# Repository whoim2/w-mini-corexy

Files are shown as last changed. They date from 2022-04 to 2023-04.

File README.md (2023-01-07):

# w-mini-corexy
small&amp;simple coreXY printer with low weight feeder and linear shafts, 238x188x150 workplace

MOD by Ahiko (recommended, standart linear bearings):
[link](https://github.com/whoim2/w-mini-corexy/tree/main/Ahiko)
or STEP assembly for solidworks:
[link](https://github.com/whoim2/w-mini-corexy/raw/main/Ahiko/Assembly1.STEP.zip)

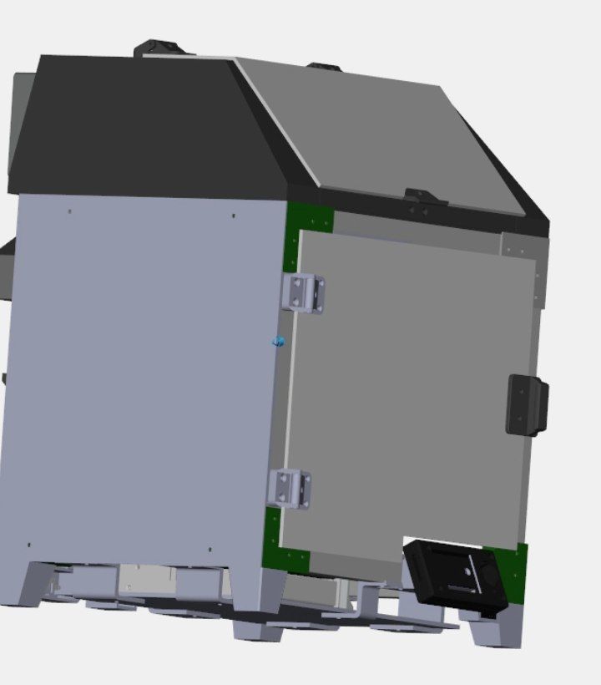
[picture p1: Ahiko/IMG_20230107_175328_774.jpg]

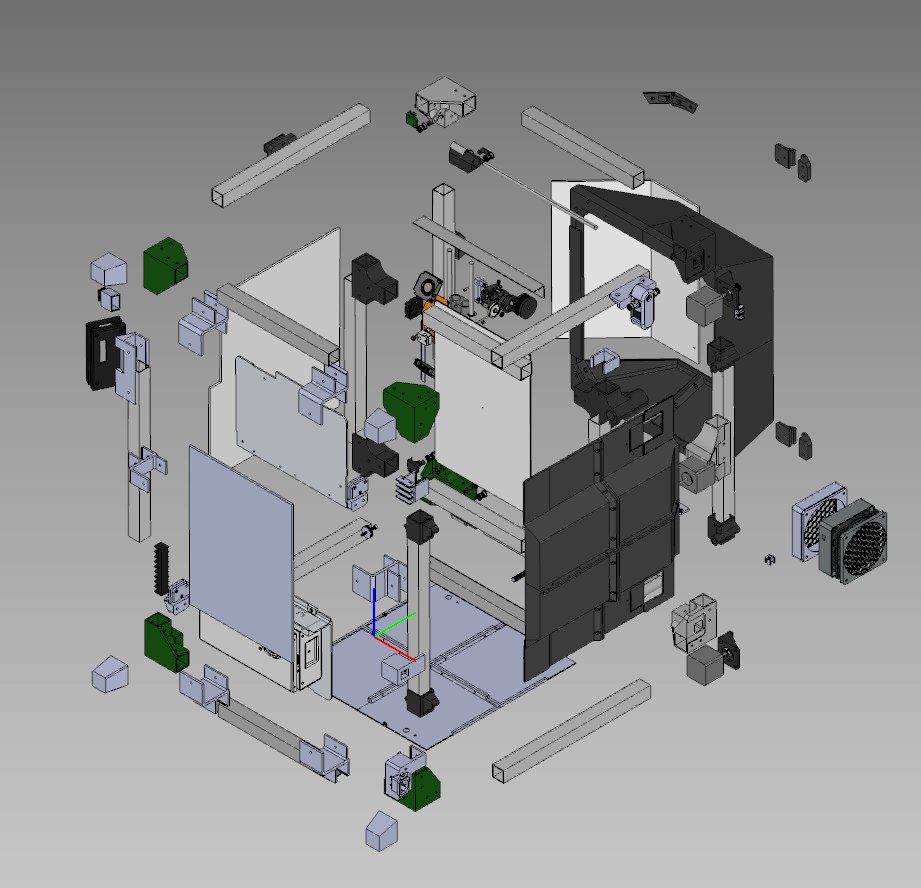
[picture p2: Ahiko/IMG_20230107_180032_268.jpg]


Original cloud files - last versions: https://disk.yandex.ru/d/OpFREoRlxXPGTw

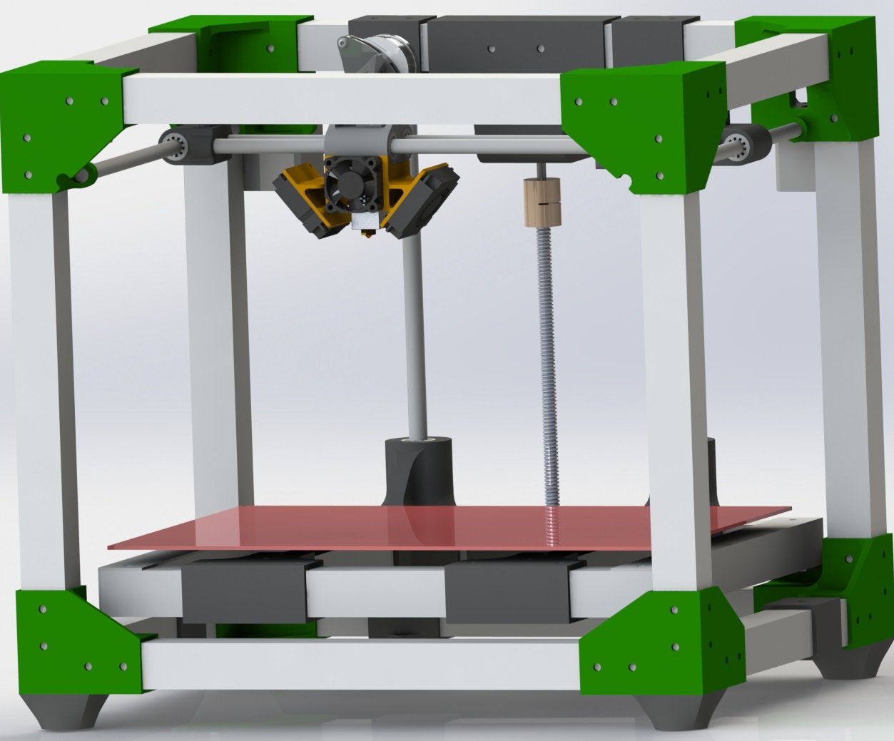
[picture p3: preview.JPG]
preview


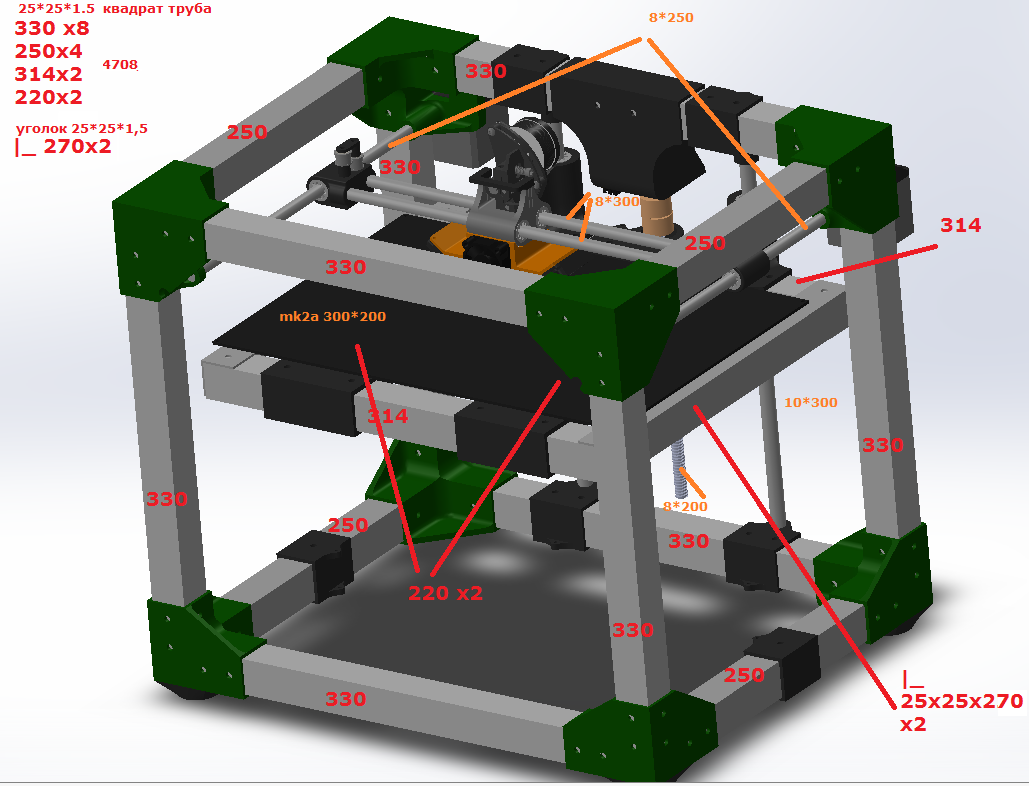
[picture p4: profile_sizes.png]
sizes


k3d mini feeder: https://github.com/dmitry-sorkin/k3d-minifeeder

[https://youtu.be/Zjof3f4mJVk](https://www.youtube.com/watch?v=Zjof3f4mJVk)

Bearings: f623zz x16

shafts: d8 L250 x2; d8 L300 x2

steppers: nema17 17HS4401S x3; Q3948-60186 x1

screw: T8 4 lead 2 pitch, 200mm, x1

rivets: d4 L8 x120

aluminum profile: 25x25x1,5 5meters

heatblock: v5 16x16x12

cut e3dv6 radiator, drill 5.5mm hole, cut M6 thread. Use offcut steel bore 3mm heatbreak for mount sink in x-carriage and teflon tube 3/2mm from feeder to heatbreak.

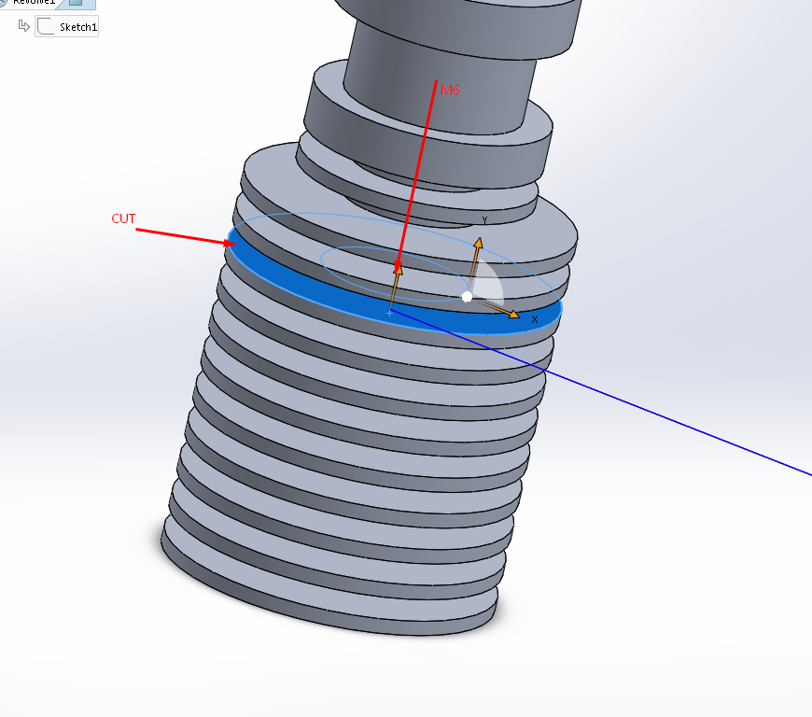
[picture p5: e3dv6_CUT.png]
cut


project in solid 2019

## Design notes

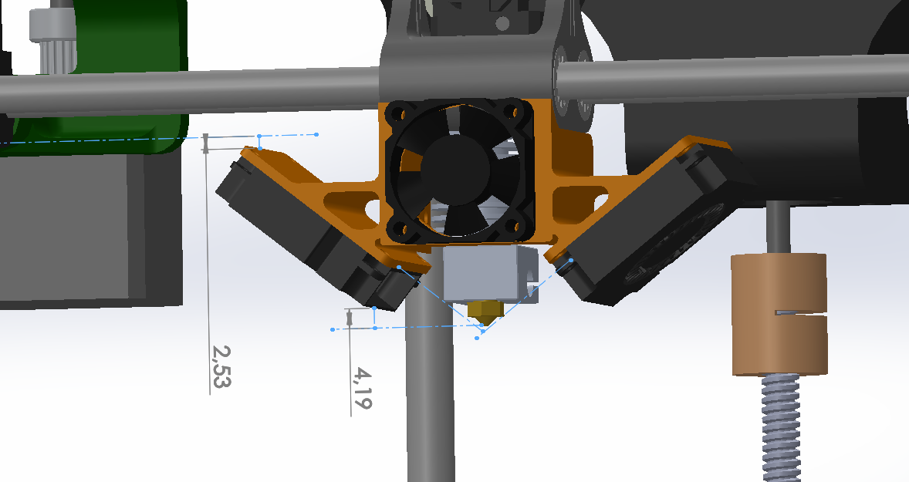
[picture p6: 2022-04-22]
Ahiko/Screenshot_1.png

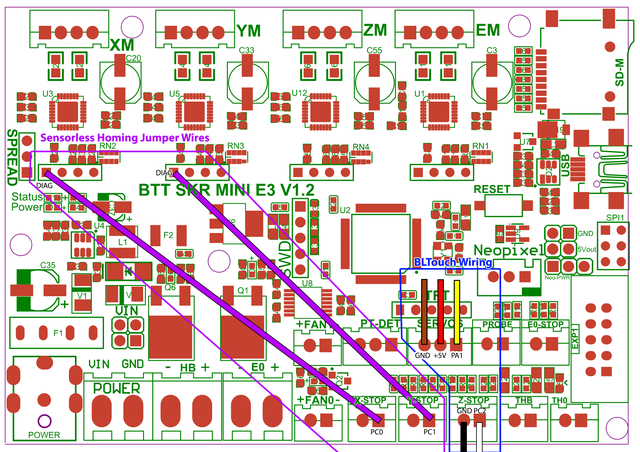
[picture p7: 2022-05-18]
klipper/skr-e3-sensorless.webp

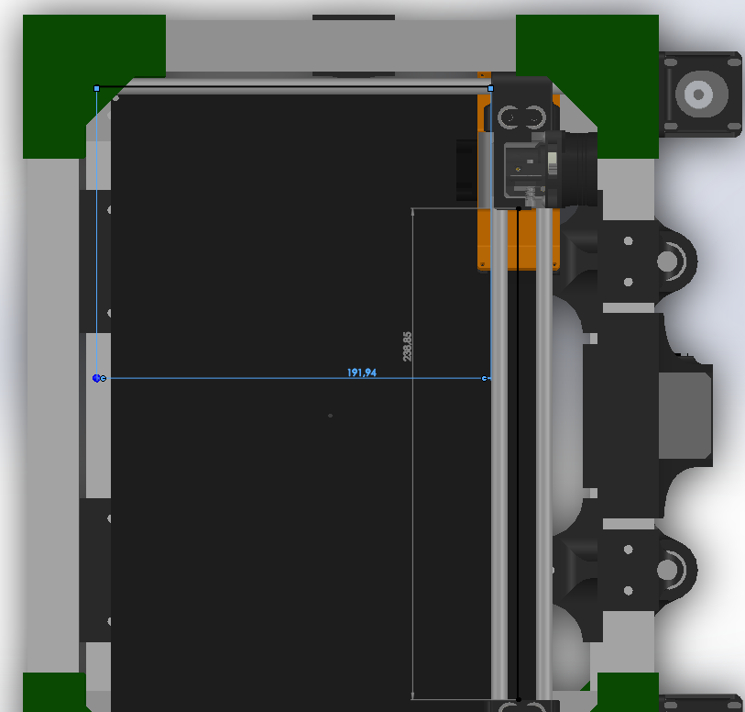
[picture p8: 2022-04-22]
Ahiko/Screenshot_2.png

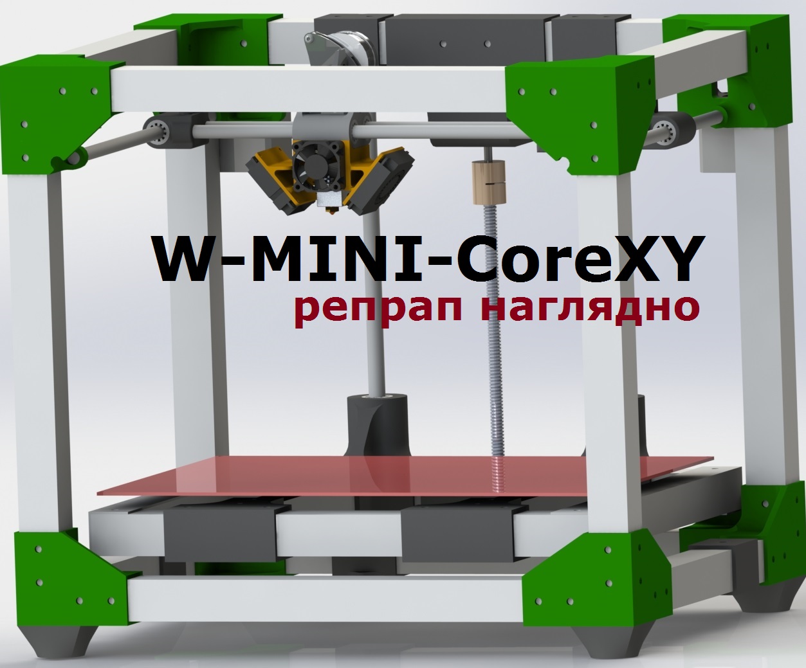
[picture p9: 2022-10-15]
Ahiko/preview_y.jpg

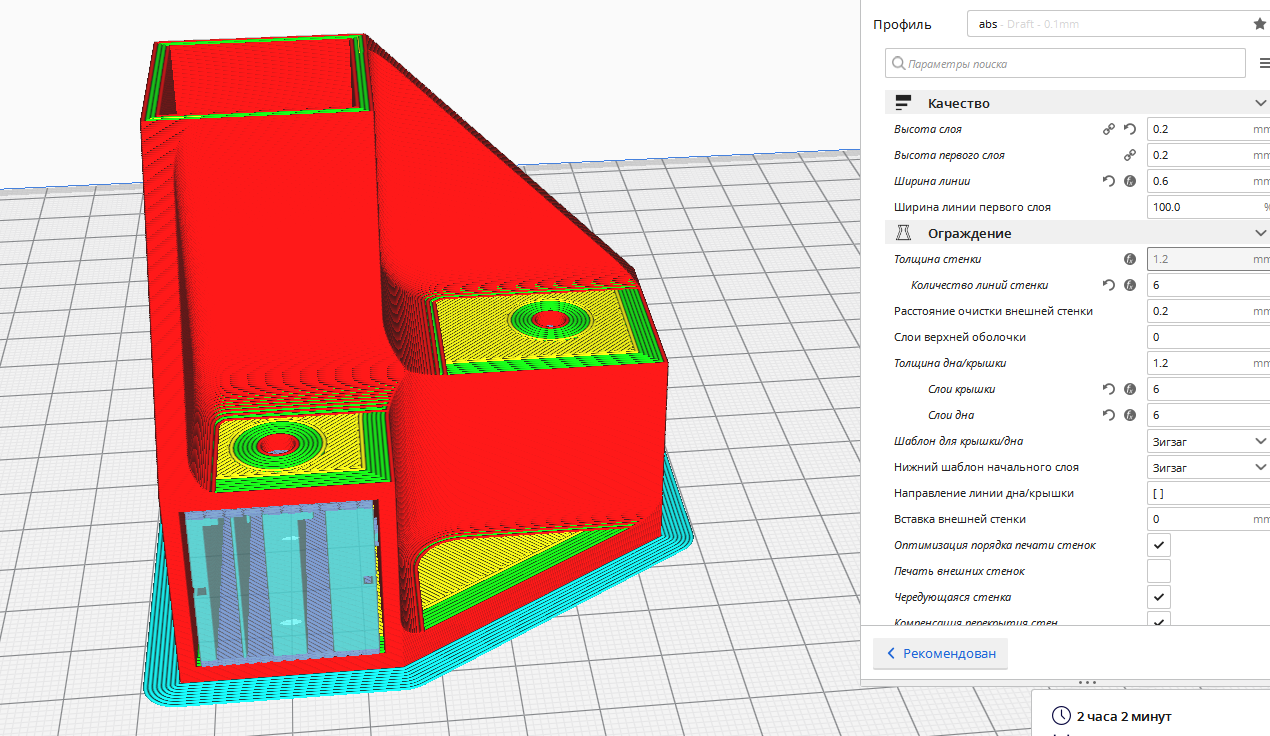
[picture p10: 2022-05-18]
Ahiko/Screenshot_3.png

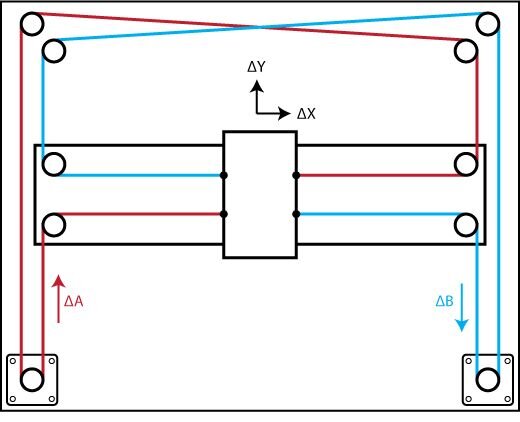
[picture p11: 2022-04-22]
Ahiko/corexy-reference_img_5eb0505acf645.jpg

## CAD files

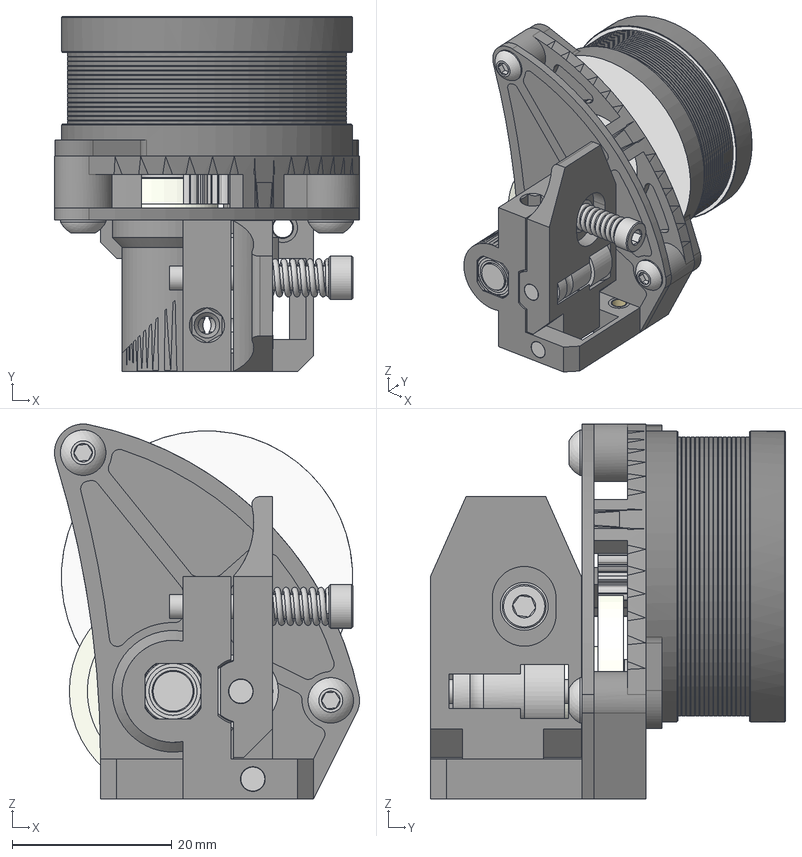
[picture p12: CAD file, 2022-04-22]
k3d-minifeeder-main/K3D Minifeeder assembly.stp
38.2 x 44.5 x 47.0 mm
MF-01b - Minifeeder back lite
MF-02b - Minifeeder front lite
Threaded insert M3x5 x 3
BMG stift 19mm x 2
Screw socket M3x20
Washer M3
BMG spring
Screw round M3x10 x 2
MF-03 - Minifeeder lever
MF-02 - Minifeeder front
MF-01 - Minifeeder back
BMG bearing x 2
Motor Nema14 L17
BMG motor gear
BMG small gear x 2

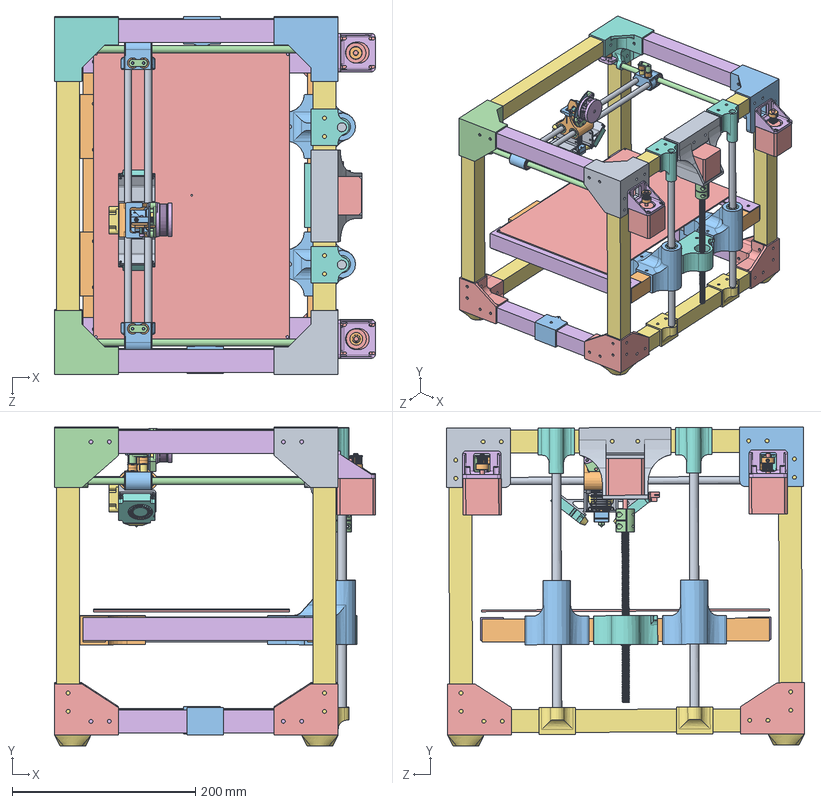
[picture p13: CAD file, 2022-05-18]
Assembly.SLDASM
350.4 x 348.1 x 390.7 mm
8x300 x 2
X_carriage
Y_carriage x 2
8x250 x 2
corner_25mm_bottom x 4
profile_sq_25x250 x 4
profile_sq_25x330 x 8
corner_25mm_top_front_1
corner_25mm_top_rear_2
f693zz x 16
corner_25mm_top_rear_1
corner_25mm_top_front_2
nema17 x 3
mot_xy_mount x 2
z_bottom_mount_linear x 2
z_top_mount_linear x 2
10x300 x 2
MF-01b - Minifeeder back lite.stp
MF-02b - Minifeeder front lite.stp
Threaded insert M3x5.stp x 3
BMG stift 19mm.stp x 2
Screw socket M3x20.stp
Washer M3.stp
BMG spring.stp
Screw round M3x10.stp x 2
MF-03 - Minifeeder lever.stp
MF-02 - Minifeeder front.stp
MF-01 - Minifeeder back.stp
BMG bearing.stp x 2
Motor Nema14 L17.stp
BMG motor gear.stp
BMG small gear.stp x 2
profile_sq_25x220 x 2
corner_25mm_Z x 2
corner_25mm_Z_bearing x 2
khop5x8
LeadScrew 8mm x 2mmPitch
LeadScrew Nut 8mm x 2mmPitch
foot x 4
mount_Z_t8nut
mount_Z_mot
profile_sq_25x314 x 2
universal_mount_25 x 2
lm8-38mm x 2
lm8-30mm x 2
front_roll_mount
bearing_roll x 4
lm10-70mm x 2
e3d-heatsink
e3d-heatbreak
e3d-heaterblock
e3d-nozzle-04
mk2a_300x200
angle_25x25_270 x 2
Fan 3010
4010blower x 2
fans_mount
GT2_16T x 2
X_carriage_topfix
bearing_roll2 x 2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

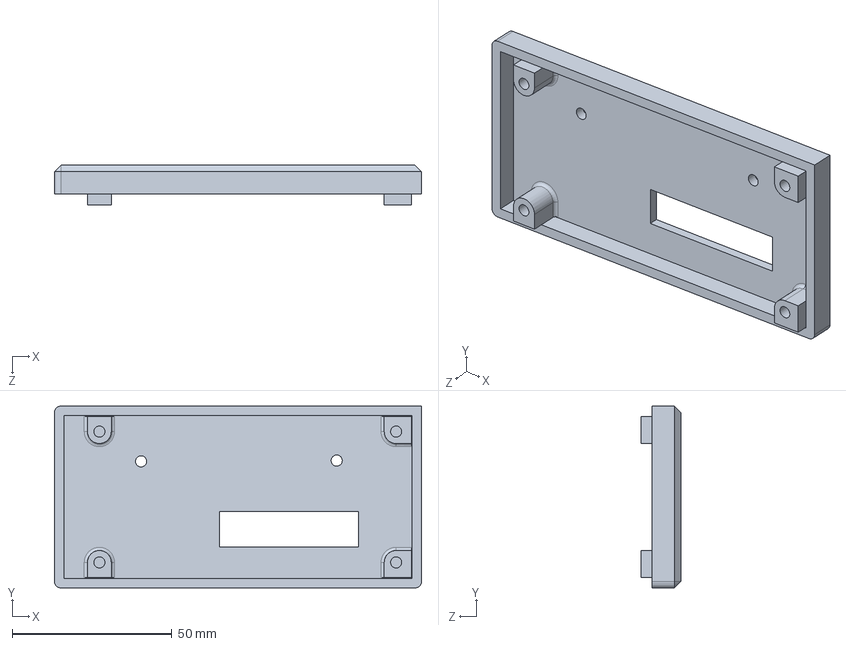
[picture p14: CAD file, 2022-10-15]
Ahiko/Сборка1.SLDASM
115.0 x 57.0 x 12.4 mm

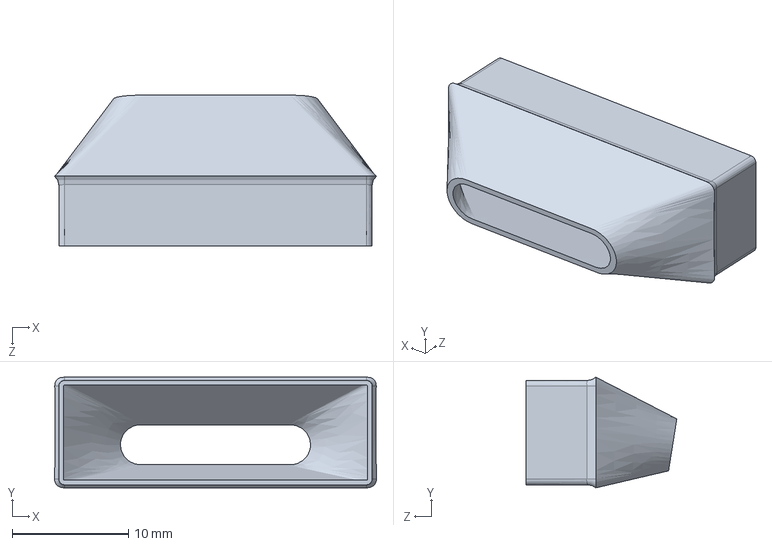
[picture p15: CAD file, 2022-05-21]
4010turbo_duct.SLDPRT
27.7 x 9.54 x 13.0 mm

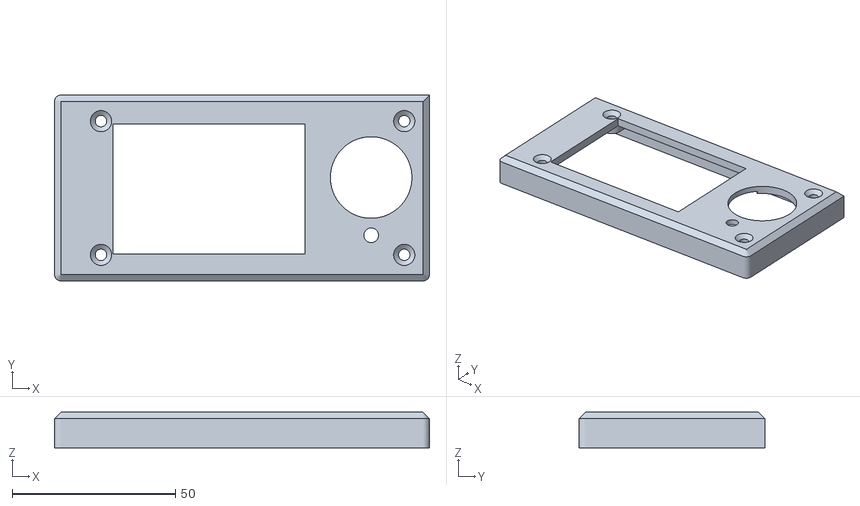
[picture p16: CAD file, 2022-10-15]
Ahiko/stl/Fysetc_Mini_12864_Mini_Front.stl
115.0 x 57.0 x 11.0

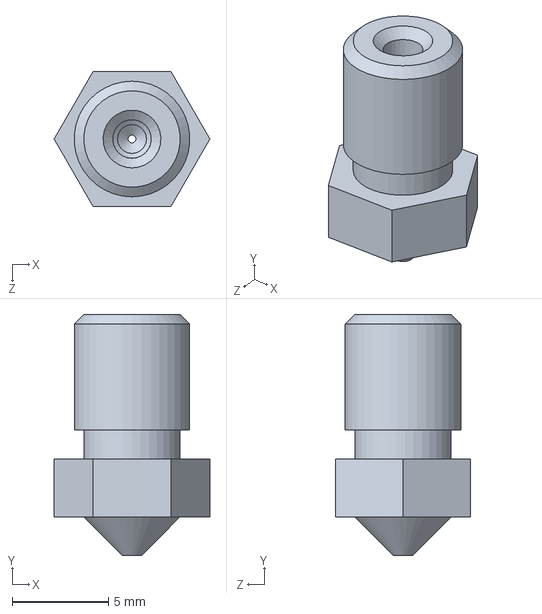
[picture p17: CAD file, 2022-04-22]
e3dv6/e3d-nozzle-04.SLDPRT
8.08 x 12.5 x 7.00 mm

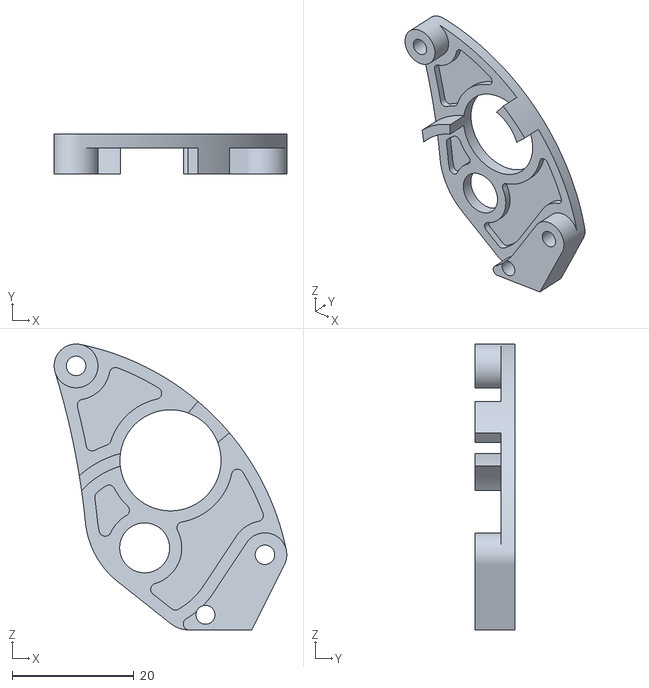
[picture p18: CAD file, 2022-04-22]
k3d-minifeeder-main/STL/K3D Minifeeder back.stl
38.2 x 6.50 x 47.0

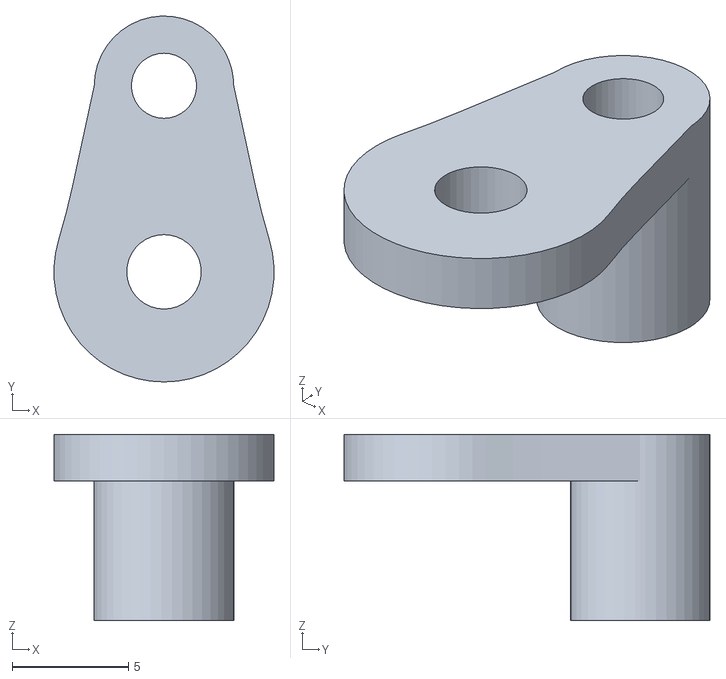
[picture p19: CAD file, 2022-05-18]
Ahiko/stl/pcb_mount.STL
9.46 x 15.7 x 8.00

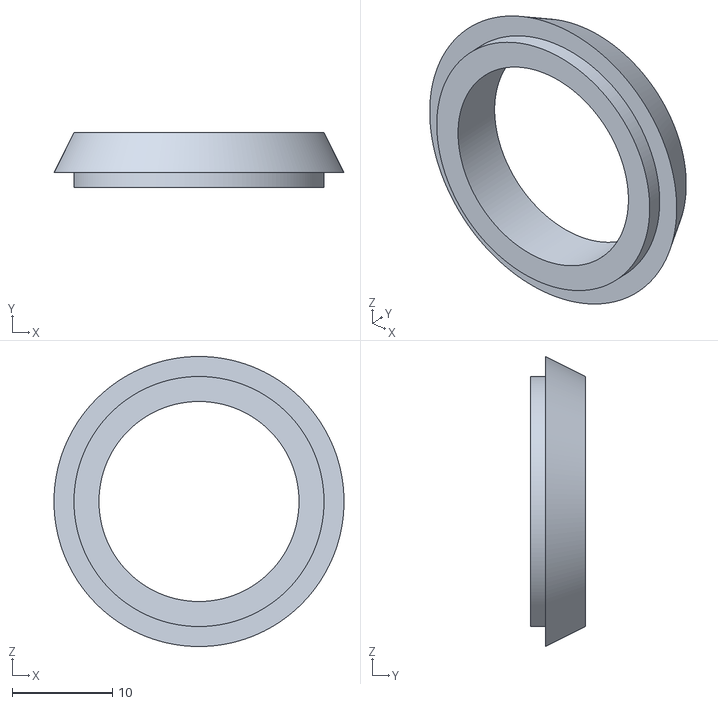
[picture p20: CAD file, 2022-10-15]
Ahiko/проставка.STL
29.0 x 5.50 x 29.0

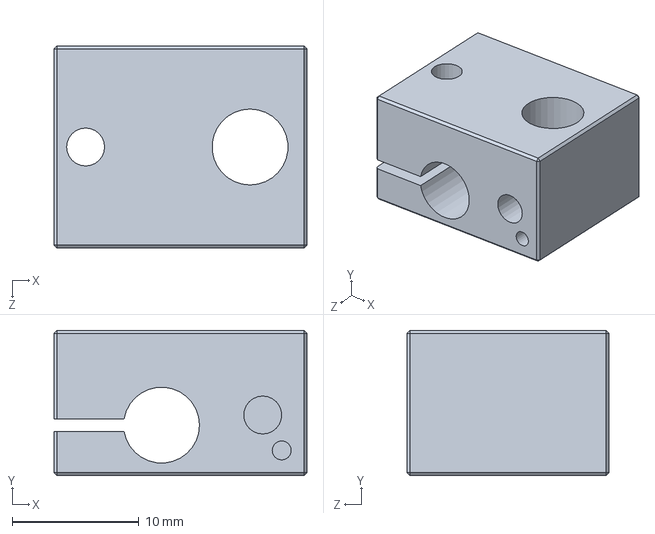
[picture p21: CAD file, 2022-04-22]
e3dv6/e3d-heaterblock.SLDPRT
20.0 x 11.5 x 16.0 mm

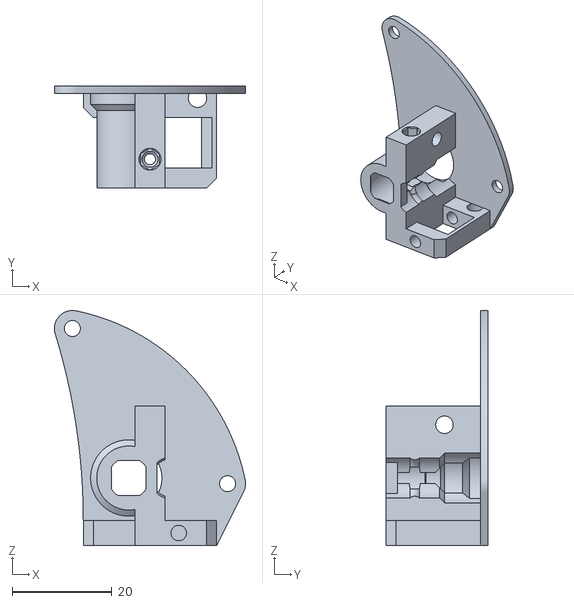
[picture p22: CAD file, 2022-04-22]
k3d-minifeeder-main/STL/K3D Minifeeder front.stl
38.2 x 20.5 x 47.0

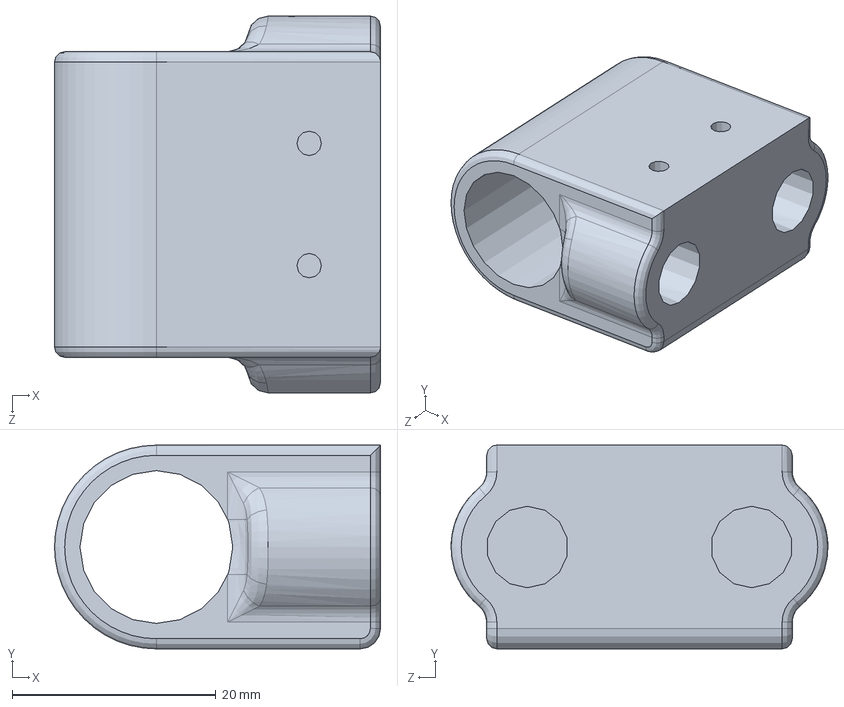
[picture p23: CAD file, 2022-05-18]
Y_carriage.SLDPRT
32.0 x 20.0 x 37.0 mm

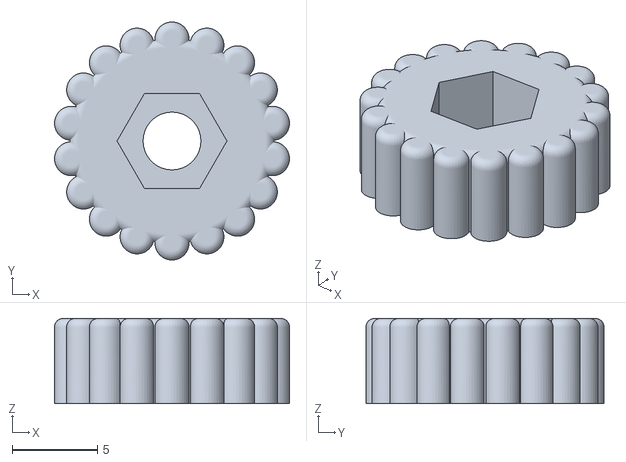
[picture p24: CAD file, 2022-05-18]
Ahiko/stl/ручка_стол.STL
13.8 x 14.0 x 5.00

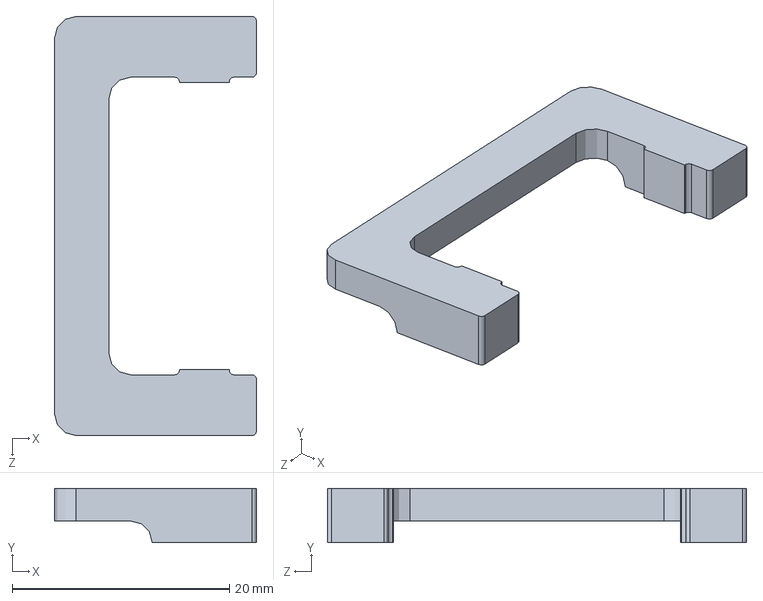
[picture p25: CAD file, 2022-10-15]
Ahiko/X_carriage_topfix.SLDPRT
18.6 x 5.00 x 38.6 mm

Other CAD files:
Ahiko/K3D Minifeeder assembly.stp.SLDASM
Ahiko/Fysetc Mini 12864 v1.step.SLDASM
e3dv6/e3d-heatbreak.SLDPRT
k3d-minifeeder-main/STL/K3D Minifeeder front lite.stl
10x300.SLDPRT
4010blower.SLDPRT
8x250.SLDPRT
8x300.SLDPRT
Ahiko/10x300.SLDPRT
Ahiko/4010blower.SLDPRT
Ahiko/4010blower.STL
Ahiko/4010turbo_duct.SLDPRT
Ahiko/4010turbo_duct.STL
Ahiko/6015fan mount.SLDPRT
Ahiko/8x250.SLDPRT
Ahiko/8x300.SLDPRT
Ahiko/Bottom.step.SLDPRT
Ahiko/Bottom_-_plain.step.SLDPRT
Ahiko/DNO.SLDPRT
Ahiko/ENDSTOP MINI 2.SLDPRT
Ahiko/Fan 3010.SLDPRT
Ahiko/Fan-Sunont_60x60x15mm.SLDPRT
Ahiko/Fysetc_12864_Display_Holder_-_HEVO.SLDPRT
Ahiko/Fysetc_12864_Display_Holder_-_HEVO.STL
Ahiko/GT2_16T.SLDPRT
Ahiko/K3D Minifeeder assembly.stp.SLDPRT
Ahiko/LCD mount.SLDPRT
Ahiko/LCD mount.STL
Ahiko/LCD mount1.STL
Ahiko/LCD mount22.SLDPRT
Ahiko/LeadScrew 8mm x 2mmPitch.SLDPRT
Ahiko/LeadScrew Nut 8mm x 2mmPitch.SLDPRT
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

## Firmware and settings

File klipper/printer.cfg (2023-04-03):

[include kiauh_macros.cfg]

[virtual_sdcard]
path: ~/gcode_files

[stepper_x]
step_pin: PB13
dir_pin: !PB12
enable_pin: !PB14
microsteps: 16
rotation_distance: 32
#endstop_pin: ^PC0
endstop_pin: tmc2209_stepper_x:virtual_endstop
position_endstop: 0
position_max: 236
homing_speed: 80
homing_retract_dist: 0

[tmc2209 stepper_x]
uart_pin: PB15
diag_pin: PC0
run_current: 1.0
#hold_current: 0.7
interpolate: false
stealthchop_threshold: 999999
driver_SGTHRS: 130

[stepper_y]
step_pin: PB10
dir_pin: !PB2
enable_pin: !PB11
microsteps: 16
rotation_distance: 32
#endstop_pin: ^PC1
endstop_pin: tmc2209_stepper_y:virtual_endstop
position_endstop: 0
position_max: 185
homing_speed: 80
homing_retract_dist: 0

[tmc2209 stepper_y]
uart_pin: PC6
diag_pin: PC1
run_current: 1.0
#hold_current: 0.7
interpolate: false
stealthchop_threshold: 999999
driver_SGTHRS: 130

[stepper_z]
step_pin: PB0
dir_pin: !PC5
enable_pin: !PB1
microsteps: 16
rotation_distance: 4
endstop_pin: ^PC2
position_min: -0.5
position_endstop: 0
position_max: 145
homing_speed: 15
homing_retract_dist: 1
second_homing_speed: 1

[tmc2209 stepper_z]
uart_pin: PC10
run_current: 0.6
#hold_current: 0.6
interpolate: false
stealthchop_threshold: 999999

[extruder]
step_pin: PB3
dir_pin: !PB4
enable_pin: !PD2
microsteps: 16
# = 200*16/steps 742
rotation_distance: 4.3126
nozzle_diameter: 0.400
filament_diameter: 1.750
heater_pin: PC8
sensor_type: ATC Semitec 104GT-2
sensor_pin: PA0
control: pid
pid_Kp: 20.348
pid_Ki: 0.898
pid_Kd: 115.221
pullup_resistor: 4700
#max_extrude_only_distance: 200
#max_extrude_only_velocity:  15
#max_extrude_only_accel: 9000
min_extrude_temp: 180
min_temp: 0
max_temp: 280
pressure_advance: 0.035
pressure_advance_smooth_time: 0.04

[tmc2209 extruder]
uart_pin: PC11
run_current: 0.400
interpolate: false
stealthchop_threshold: 999999

[firmware_retraction]
retract_length: 0.6
retract_speed: 25
#unretract_extra_length: 0.02
unretract_speed: 20

[probe]
pin: ^!PC14
speed: 5.0
#x_offset: 0.0
#   The distance (in mm) between the probe and the nozzle along the
#   x-axis. The default is 0.
#y_offset: 0.0
#   The distance (in mm) between the probe and the nozzle along the
#   y-axis. The default is 0.
z_offset: 0.1
#   The distance (in mm) between the bed and the nozzle when the probe
#   triggers. This parameter must be provided.
samples: 5
#   The number of times to probe each point. The probed z-values will
#   be averaged. The default is to probe 1 time.
sample_retract_dist: 2.0
#   The distance (in mm) to lift the toolhead between each sample (if
#   sampling more than once). The default is 2mm.
lift_speed: 3.0
#   Speed (in mm/s) of the Z axis when lifting the probe between
#   samples. The default is to use the same value as the 'speed'
#   parameter.
samples_result: average
#   The calculation method when sampling more than once - either
#   "median" or "average". The default is average.
samples_tolerance: 0.100
#   The maximum Z distance (in mm) that a sample may differ from other
#   samples. If this tolerance is exceeded then either an error is
#   reported or the attempt is restarted (see
#   samples_tolerance_retries). The default is 0.100mm.
samples_tolerance_retries: 2
#   The number of times to retry if a sample is found that exceeds
#   samples_tolerance. On a retry, all current samples are discarded
#   and the probe attempt is restarted. If a valid set of samples are
#   not obtained in the given number of retries then an error is
#   reported. The default is zero which causes an error to be reported
#   on the first sample that exceeds samples_tolerance.

[heater_bed]
heater_pin: PC9
sensor_type: Generic 3950
sensor_pin: PC3
control: pid
pid_Kp: 64.986
pid_Ki: 1.647
pid_Kd: 640.925
min_temp: 0
max_temp: 111

[fan]
pin: PC12
max_power: 0.65

[mcu]
serial: /dev/ttyAMA0
restart_method: command

[printer]
kinematics: corexy
max_velocity: 200
max_accel: 3000
max_z_velocity: 15
max_z_accel: 20
square_corner_velocity: 8

[static_digital_output usb_pullup_enable]
pins: !PC13

[board_pins]
aliases:
    # EXP1 header
    EXP1_1=PB5, EXP1_3=PA9,   EXP1_5=PA10, EXP1_7=PB8, EXP1_9=<GND>,
    EXP1_2=PB6, EXP1_4=<RST>, EXP1_6=PB9,  EXP1_8=PB7, EXP1_10=<5V>

# See the sample-lcd.cfg file for definitions of common LCD displays.

[gcode_arcs]
resolution: 1.0
#   An arc will be split into segments. Each segment's length will
#   equal the resolution in mm set above. Lower values will produce a
#   finer arc, but also more work for your machine. Arcs smaller than
#   the configured value will become straight lines. The default is
#   1mm.

[input_shaper]
shaper_type: mzv
shaper_freq_x: 0
shaper_freq_y: 0

[temperature_sensor RPi]
sensor_type: temperature_host
min_temp: 10
max_temp: 100
gcode_id: PI


[filament_switch_sensor my_sensor]
pause_on_runout: True
#runout_gcode:
#insert_gcode:
#event_delay: 3.0
#pause_delay: 0.5
switch_pin: ^!PC15 #e0-endstop


#################################
############## LED ##############

[neopixel my_led]
pin: PC7
chain_count: 18
initial_RED: 0.5
initial_GREEN: 0.5
initial_BLUE: 0.5
[include led_progress.cfg]

############## MARLIN MACROS ##############

[gcode_macro M900]
gcode:
  {% if 'K' in params %}
    {% if 'E' in params %}
      SET_PRESSURE_ADVANCE EXTRUDER={params.E} ADVANCE={params.K}
    {% else %}
      SET_PRESSURE_ADVANCE ADVANCE={params.K}
    {% endif %}
  {% endif %}

############## POWER OFF ##############

[gcode_macro M81] #Power off
gcode:
      SET_PIN PIN=Power VALUE=1
      
[gcode_macro M80] #Power on
gcode:
      SET_PIN PIN=Power VALUE=0
      
[output_pin Power]
pin: PA1
value:0
shutdown_value:1

############## TIMEOUT IDLE ##############

[idle_timeout]
gcode:
  TURN_OFF_HEATERS
  M84
  LED_NIGHT
timeout: 900

############## HOMING ##############

[gcode_macro SENSORLESS_HOME_X]
gcode:
    {% set HOME_CUR = 0.900 %}
    {% set driver_config = printer.configfile.settings['tmc2209 stepper_x'] %}
    {% set RUN_CUR = driver_config.run_current %}
    {% set HOLD_CUR = driver_config.hold_current %}
    SET_TMC_CURRENT STEPPER=stepper_x CURRENT={HOME_CUR} HOLDCURRENT={HOME_CUR}
    G4 P1000
    G28 X0
    G90
    G1 X5 F1200   # Move X to safe X
    SET_TMC_CURRENT STEPPER=stepper_x CURRENT={RUN_CUR} HOLDCURRENT={HOLD_CUR}

[gcode_macro SENSORLESS_HOME_Y]
gcode:
    {% set HOME_CUR = 0.900 %}
    {% set driver_config = printer.configfile.settings['tmc2209 stepper_y'] %}
    {% set RUN_CUR = driver_config.run_current %}
    {% set HOLD_CUR = driver_config.hold_current %}
    SET_TMC_CURRENT STEPPER=stepper_y CURRENT={HOME_CUR} HOLDCURRENT={HOME_CUR}
    G4 P1000
    G28 Y0
    G1 Y5 F1200   # Move Y to safe X
    SET_TMC_CURRENT STEPPER=stepper_y CURRENT={RUN_CUR} HOLDCURRENT={HOLD_CUR}

[force_move]
enable_force_move: True

[homing_override]
axes: xyz
gcode:
    G90 #absolute
    {% set flag_O = params.O|default("false") %}
    {% set flag_X = params.X|default("false") %}
    {% set flag_Y = params.Y|default("false") %}
    {% set flag_Z = params.Z|default("false") %}
    {% if (flag_Y == "false" and flag_X == "false" and flag_Z == "false") %}
        {% set flag_X = "true" %}
        {% set flag_Y = "true" %}
        {% set flag_Z = "true" %}
    {% endif %}
    {% if flag_O !="false" and 'x' in printer.toolhead.homed_axes %}
        {% set flag_X = "false" %}
    {% endif %}
    {% if flag_O !="false" and 'y' in printer.toolhead.homed_axes %}
        {% set flag_Y = "false" %}
    {% endif %}
    {% if flag_O !="false" and 'z' in printer.toolhead.homed_axes %}
        {% set flag_Z = "false" %}
    {% endif %}
    
    {% if (flag_X !="false" or flag_Y !="false" or flag_Z !="false") %}
        {% if 'z' not in printer.toolhead.homed_axes %}
            #FORCE_MOVE STEPPER=stepper_z DISTANCE=5 VELOCITY=10 # Raise Z
        {% else %}
            G91 # relative
            G0 Z5 F600
            G90 # absolute
        {% endif %}
    {% endif %}
    {% if (flag_Y != "false") or ((flag_X != "false" or flag_Z != "false") and 'y' not in printer.toolhead.homed_axes) %}
         SENSORLESS_HOME_Y
    {% endif %}
    {% if (flag_X != "false") or (flag_Z != "false" and 'x' not in printer.toolhead.homed_axes) %}
         G0 Y5 F3000  # Move Y to safe X
         SENSORLESS_HOME_X
    {% endif %}
    {% if flag_Z != "false" %}
    #     {% set bltouch = printer.configfile.settings['bltouch'] %}
    #     G0 X{200 - bltouch.x_offset} Y{195 - bltouch.y_offset} F3600 #Move XY to safe Z
         G28 Z
         G0 Z10 F1800  
    {% endif %}

[display]
lcd_type: ssd1306
i2c_bus: i2c1a
i2c_mcu = mcu
encoder_pins: ^PA10, ^PA9
click_pin: ^!PB7

[menu __main __octoprint __poweroff]
type: command
name: Turn off Octopi
gcode:
    {action_call_remote_method("shutdown_machine")}

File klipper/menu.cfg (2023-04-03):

# This file defines the default layout of the printer's menu.

# It is not necessary to edit this file to change the menu. Instead,
# one may override any of the sections defined here by defining a
# section with the same name in the main printer.cfg config file.

### DEFAULT MENU ###
# Main
#   + Tune
#       + Speed: 000%
#       + Flow: 000%
#       + Offset Z:00.00
#   + OctoPrint
#       + Pause printing
#       + Resume printing
#       + Abort printing
#   + SD Card
#       + Start printing
#       + Resume printing
#       + Pause printing
#       + Cancel printing
#       + ... (files)
#   + Control
#       + Home All
#       + Home Z
#       + Home X/Y
#       + Steppers off
#       + Fan: OFF
#       + Fan speed: 000%
#       + Lights: OFF
#       + Lights: 000%
#       + Move 10mm
#           + Move X:000.0
#           + Move Y:000.0
#           + Move Z:000.0
#           + Move E:+000.0
#       + Move 1mm
#           + Move X:000.0
#           + Move Y:000.0
#           + Move Z:000.0
#           + Move E:+000.0
#       + Move 0.1mm
#           + Move X:000.0
#           + Move Y:000.0
#           + Move Z:000.0
#           + Move E:+000.0
#   + Temperature
#       + Ex0:000 (0000)
#       + Ex1:000 (0000)
#       + Bed:000 (0000)
#       + Preheat PLA
#           + Preheat all
#           + Preheat hotend
#           + Preheat hotbed
#       + Preheat ABS
#           + Preheat all
#           + Preheat hotend
#           + Preheat hotbed
#       + Cooldown
#           + Cooldown all
#           + Cooldown hotend
#           + Cooldown hotbed
#   + Filament
#       + Ex0:000 (0000)
#       + Load Fil. fast
#       + Load Fil. slow
#       + Unload Fil.fast
#       + Unload Fil.slow
#       + Feed: 000.0
#   + Setup
#       + Save config
#       + Restart
#           + Restart host
#           + Restart FW
#       + PID tuning
#           + Tune Hotend PID
#           + Tune Hotbed PID
#       + Calibration
#           + Delta cal. auto
#           + Delta cal. man
#               + Start probing
#               + Move Z: 000.00
#               + Test Z: ++
#               + Accept
#               + Abort
#           + Bed probe
#       + Dump parameters

### menu main ###
[menu __main]
type: list
name: Main

### menu tune ###
[menu __main __tune]
type: list
enable: {printer.idle_timeout.state == "Printing"}
name: Tune

[menu __main __tune __speed]
type: input
name: Speed: {'%3d' % (menu.input*100)}%
input: {printer.gcode_move.speed_factor}
input_min: 0.01
input_max: 5
input_step: 0.01
realtime: True
gcode:
    M220 S{'%d' % (menu.input*100)}

[menu __main __tune __flow]
type: input
name: Flow: {'%3d' % (menu.input*100)}%
input: {printer.gcode_move.extrude_factor}
input_min: 0.01
input_max: 2
input_step: 0.01
realtime: True
gcode:
    M221 S{'%d' % (menu.input*100)}

[menu __main __tune __offsetz]
type: input
name: Offset Z:{'%05.3f' % menu.input}
input: {printer.gcode_move.homing_origin.z}
input_min: -5
input_max: 5
input_step: 0.005
realtime: True
gcode:
    SET_GCODE_OFFSET Z={'%.3f' % menu.input} MOVE=1


### menu octoprint ###
[menu __main __octoprint]
type: list
name: OctoPrint

[menu octoprint poweroff]
type: command
enable: !toolhead.is_printing
name: Turn off Pi
gcode:
    {action_respond_info('action:poweroff')}

[menu __main __octoprint __pause]
type: command
enable: {printer.idle_timeout.state == "Printing"}
name: Pause printing
gcode:
    {action_respond_info('action:pause')}

[menu __main __octoprint __resume]
type: command
enable: {not printer.idle_timeout.state == "Printing"}
name: Resume printing
gcode:
    {action_respond_info('action:resume')}

[menu __main __octoprint __abort]
type: command
enable: {printer.idle_timeout.state == "Printing"}
name: Abort printing
gcode:
    {action_respond_info('action:cancel')}

### menu virtual sdcard ###
[menu __main __sdcard]
type: vsdlist
enable: {('virtual_sdcard' in printer)}
name: SD Card

[menu __main __sdcard __start]
type: command
enable: {('virtual_sdcard' in printer) and printer.virtual_sdcard.file_path and not printer.virtual_sdcard.is_active}
name: Start printing
gcode: M24

[menu __main __sdcard __resume]
type: command
enable: {('virtual_sdcard' in printer) and printer.print_stats.state == "paused"}
name: Resume printing
gcode:
    {% if "pause_resume" in printer %}
        RESUME
    {% else %}
        M24
    {% endif %}

[menu __main __sdcard __pause]
type: command
enable: {('virtual_sdcard' in printer) and printer.print_stats.state == "printing"}
name: Pause printing
gcode:
    {% if "pause_resume" in printer %}
        PAUSE
    {% else %}
        M25
    {% endif %}
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

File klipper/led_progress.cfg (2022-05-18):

# use NEOPIXEL_DISPLAY LED=Led_Name TYPE=template_type MODE=template_mode

# for TYPE use:
# extruder_temp     :extruder temperature progress
# bed_temp          :bed temperature progress
# print_percent     :print progress
# printer_speed     :printer speed

# for MODE use:
# progress          :the leds will light up one by one
# glow              :all leds will fade from one color (or non) to other color

# more info: https://github.com/digitalninja-ro/klipper-neopixel/blob/master/README.md

[gcode_macro LED_OFF]
gcode:
  SET_LED_TEMPLATE LED=my_led TEMPLATE=
  SET_LED LED=my_led RED=0 GREEN=0 BLUE=0

[gcode_macro LED_WHITE]
gcode:
  SET_LED_TEMPLATE LED=my_led TEMPLATE=
  SET_LED LED=my_led RED=1 GREEN=1 BLUE=1

[gcode_macro LED_RED]
gcode:
  SET_LED_TEMPLATE LED=my_led TEMPLATE=
  SET_LED LED=my_led RED=1 GREEN=0 BLUE=0

[gcode_macro LED_GREEN]
gcode:
  SET_LED_TEMPLATE LED=my_led TEMPLATE=
  SET_LED LED=my_led RED=0 GREEN=1 BLUE=0

[gcode_macro LED_NIGHT]
gcode:
  SET_LED_TEMPLATE LED=my_led TEMPLATE=
  SET_LED LED=my_led RED=0 GREEN=0 BLUE=0.1

[gcode_macro LED_PROGRESS]
gcode:
  NEOPIXEL_DISPLAY LED="my_led" TYPE=print_percent MODE=glow


[gcode_macro NEOPIXEL_DISPLAY]
gcode:
    {% set led = params.LED %}
    {% set type = params.TYPE %}
    {% set mode = params.MODE %}
    {% set my_neopixel = printer.configfile.config['neopixel ' ~ led] %}

    {% if mode == 'progress' %}
        {% for i in range(my_neopixel.chain_count|int) %}
            SET_LED_TEMPLATE LED={led} INDEX={i+1} TEMPLATE={'led_' ~ type ~ '_' ~ mode} param_led_num={i+1} param_led_total={my_neopixel.chain_count|int}
        {% endfor %}
    {% endif %}
    {% if mode == 'glow' %}
        SET_LED_TEMPLATE LED={led} TEMPLATE={'led_' ~ type ~ '_' ~ mode}
    {% endif %}

[display_template led_extruder_temp_glow]
text:
    {% if printer.extruder.target > 0.0 %}
        {%  set temp = printer.extruder.target %}
    {% else %}
        {% set temp = printer.configfile.config.extruder.max_temp %}
    {% endif %}
    {% set ratio = printer.extruder.temperature / temp|float %}
    {ratio}, 0.0, {1-ratio}, 0.0

[display_template led_extruder_temp_progress]
param_led_num:  0
param_led_total: 1
text:
    {% if printer.extruder.target > 0.0 %}
        {%  set temp = printer.extruder.target %}
    {% else %}
        {% set temp = printer.configfile.config.extruder.max_temp %}
    {% endif %}
    {% set ratio = printer.extruder.temperature / temp|float %}
    {% set led_ratio = param_led_num|float / param_led_total %}
    {% if ratio > led_ratio %}
        {led_ratio}, 0.0, 0.0, 0.0
    {% else %}
        0.0, 0.0, 0.0, 0.0
    {% endif %}

[display_template led_bed_temp_glow]
text:
    {% if printer.heater_bed.target > 0.0 %}
        {%  set temp = printer.heater_bed.target %}
    {% else %}
        {% set temp = printer.configfile.config.heater_bed.max_temp %}
    {% endif %}
    {% set ratio = printer.heater_bed.temperature / temp|float %}
    {ratio}, 0.0, {1-ratio}, 0.0

[display_template led_bed_temp_progress]
param_led_num:  0
param_led_total: 1
text:
    {% if printer.heater_bed.target > 0.0 %}
        {%  set temp = printer.heater_bed.target %}
    {% else %}
        {% set temp = printer.configfile.config.heater_bed.max_temp %}
    {% endif %}
    {% set ratio = printer.heater_bed.temperature / temp|float %}
    {% set led_ratio = param_led_num|float / param_led_total %}
    {% if ratio > led_ratio %}
        {led_ratio}, 0.0, 0.0, 0.0
    {% else %}
        0.0, 0.0, 0.0, 0.0
    {% endif %}

[display_template led_print_percent_glow]
text:
    {% set ratio = printer.virtual_sdcard.progress %}
    0.0, {ratio}, 0.0, 0.0

[display_template led_print_percent_progress]
param_led_num:  0
param_led_total: 1
text:
    {% set ratio = printer.virtual_sdcard.progress %}
    {% set led_ratio   = param_led_num|float / param_led_total %}
    {% if ratio > led_ratio %}
        0.0, {led_ratio}, 0.0, 0.0
    {% else %}
        0.0, 0.0, 0.0, 0.0
    {% endif %}

[display_template led_printer_speed_glow]
text:
    {% set ratio  = printer.motion_report.live_velocity|float /  printer.configfile.config.printer.max_velocity|float %}
    0.0, {ratio}, 0.0, 0.0

[display_template led_printer_speed_progress]
param_led_num:  0
param_led_total: 1
text:
    {% set ratio  = printer.motion_report.live_velocity|float /  printer.configfile.config.printer.max_velocity|float %}
    {% set led_ratio    = param_led_num|float / param_led_total %}
    {% if ratio > led_ratio %}
        0.0, {led_ratio}, 0.0, 0.0
    {% else %}
        0.0, 0.0, 0.0, 0.0
    {% endif %}
